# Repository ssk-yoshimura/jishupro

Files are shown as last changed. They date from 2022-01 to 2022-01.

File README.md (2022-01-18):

# 腱之介（けんのすけ）
自主プロ2021のために製作した、ワイヤー駆動ロボット



発表スライド：

https://github.com/ssk-yoshimura/jishupro/blob/master/kennosuke_.pdf

#### アピールポイント

- 6自由度を筋肉10本で動かすロボット（足回り2輪付き）
- 機構を工夫し、安いモータで大きなロボットを動かす（ロボットアーム長0.5m）
- IKを解き、関節角度軌道->ワイヤー長軌道(非線形)を計算して追従&モータの協調動作を実現
- 画像認識も行っている

#### できること
- 歩行（前進、後退、回転）
- 認識（お手）

## メカ構成
基本的に、3Dプリンタとレーザー加工機で製作。骨組み等はホームセンターで入手可能で安価なものを利用。

モータは秋月の連続回転サーボ（エンコーダ付き）FB5311M-360を使用。
- 根本にアクチュエータを集約し、ロボットアームを軽量化
- 肩関節は2自由度3ワイヤー、肘関節は1自由度2ワイヤー
- 両腕と足回り2輪で、合計12個のモータを使用
- モーメントアームを大きくし、減速比を上げてトルクを大きくした。

## 回路構成
- ESP32を使用
- 秋月のI2C接続16チャンネル　サーボ＆ＰＷＭ駆動キットを使用
- 電源は5v4AのACアダプターx2

## ソフトウェア構成
ROSを使用し、IK等にはEusLispを利用した。次のような順番で処理を行っている。

1. (python)Coral TPUからPoseArrayトピックをサブスクライブし、人の姿勢の判別等を行ったり、カメラ画像の色で画像処理を行ったりする。実際はAction Serverとして、呼び出された時のみ処理を行う
3. (euslisp)画像認識の場合はAction Clientとなって利用
4. (euslisp)ロボット手先の軌道を作成
5. (euslisp)手先の軌道をもとにIKを解き、関節角度軌道を作成
6. (euslisp)関節角度軌道から順運動学でワイヤー長軌道を作成(関節角度とワイヤー長は非線形)
7. (euslisp)ワイヤー長軌道と時間、制御パラメータ等をまとめたものを分割し、Float32MultiArrayトピックとしてESP32に送る
8. (ESP32)受信した軌道に欠落がないことを確認し、モータの角度軌道に変換
9. (ESP32)モータの角度軌道をもとに、エンコーダのフィードバックを使って追従制御&協調して動作させる

CAD(SolidWorks)で設計したデータをもとにURDFファイルを作成し、STLを貼り付けた。これを使用して、eusのビューワやRvizでシミュレーションを行った。eusはURDF,yamlから変換してロボットモデルを自動生成した。

#### サーボの初期化
特定の姿勢の状態で、ワイヤーを手動で張り詰めた状態にする。このときのアブソリュートエンコーダの値を読み、サーボ角度とワイヤー長の関係を得る。

使用時は、まずこの初期化のプログラム実行してから、PCとの通信・制御等のプログラムを実行する。

# 発表実演手順
### 準備
```
roscore
```
#### wire_initializeスケッチ
- 電源は外し、init_pinも外して書き込む
- リセットボタンを押す->電源つける->init_pinつける
- シリアルモニタで異常なしを確認、値をコピー
#### wire_pullスケッチ
- コピーした値を貼り付ける
- 電源は外し、init_pinも外して書き込む
- リセットボタンを押す->電源つける->init_pinつける
```
rosrun rosserial_python serial_node.py
```
#### euslisp
jishupro/euslispに入る
```
emacs demo.l
```
シェルを開いて
```
roseus "demo.l
```
```
walk-prepare
```
#### USBカメラ 
ここで初めて、カメラとCoralを付ける。
- フリーズした場合、カメラを挿し直すと改善することがある。

```ls /dev/video```でvideo1があることを確認する。

```
rosrun uvc_camera uvc_camera_node _device:=/dev/video1
```

- PCのカメラの場合```rosrun usb_cam usb_cam_node```

#### Edge TPU 
```
source /opt/ros/melodic/setup.bash
```
```
source ~/coral_ws/devel/setup.bash
```
```
roslaunch coral_usb edgetpu_human_pose_estimator.launch INPUT_IMAGE:=/image_raw
```
#### Action Server
```
python cv_pose_action.py
```
### 発表
#### eusプログラム
- walk-prepare
- walk-both
- walk-back
- rotate
- yc

# リンク集
#### eusモデル、関数など
https://github.com/ssk-yoshimura/jishupro/tree/master/jishupro#readme
#### 諸注意など
https://github.com/ssk-yoshimura/jishupro/tree/master/jishupro/euslisp#readme
#### エンコーダ付き連続回転サーボの処理
https://github.com/ssk-yoshimura/jishupro/tree/master/jishupro/sketch/PCA9685_Sample5#readme

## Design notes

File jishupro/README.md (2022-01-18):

# 腱之介のeusモデル

eusでは```*mbot*```という名前

## 関節
本体側から順
- ```:rarm-shoulder-y```
- ```:rarm-shoulder-p```
- ```:rarm-elbow-p```
- ```:larm-shoulder-y```
- ```:larm-shoulder-p```
- ```:larm-elbow-p```

使用例

```
(send *mbot* :rarm-shoulder-y :joint-angle -30)
```

## 末端
- ```:rarm-end-coords```
- ```:larm-end-coords```

使用例

```
(send *mbot* :rarm-end-coords)
```
または
```
(send *mbot* :rarm :end-coords)
```

## ポーズ
- ```:zero-pose```
- ```:open-pose```
- ```:init-pose``` (サーボ・ワイヤーの初期化用）

使用例

```
(send *mbot* :init-pose)
```
## 関数
重要なもののみ

### ワイヤー関数
```
(load "mbot-utils.l")
(send *mbot* :wire-init) ;; 初期化時に必ず呼ぶ
(send *mbot* :wire-calc) ;; ワイヤー長計算時に必ず呼ぶ
(draw-wire-end) ;; ワイヤー中継地点、関節などを描画
```
### 軌道生成関数
```mbot-ri.l```の関数
```
mbot2ri-avs (avs wheels time_all sequence_mode &key thre_dist goal_offset)
```
引数：関節角度軌道、ホイールの角度軌道、時間、軌道追従の方式、収束判定の閾値、軌道追従のパラメータ

機能：関節角度軌道をワイヤー長軌道に変換し、ESP32に送る

```traj.l```の関数
```
mbot2ri-avs-ik (rtarget ltarget wrtarget wltarget time_all sequence_mode &key thre_dist goal_offset)
```
引数：手のik目標、ホイールの目標、時間、軌道追従の方式、収束判定の閾値、軌道追従のパラメータ

機能：目標をもとにikを解いて軌道を生成し、ESP32に送る

### デモ用の関数
```load "demo.l```でデモに必要な全てのeusプログラムがロードされる
- ```walk-prepare``` 歩行用の姿勢にする
- ```walk-prepare 1```歩行用の姿勢から初期状態へ戻す
- ```walk-both```歩行
- ```walk-back```後ろ向きに歩行
- ```rotate```回転
- ```yc```認識のAction Client（二回行う）

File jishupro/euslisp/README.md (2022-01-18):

## ESP32のプログラム起動の諸注意
- モータの電源を抜き、init_pinを繋げない状態で書き込む。
- リセットボタンを押してから、モータの電源を入れて、その後init_pinを繋げる。
- rosrun rosserial_...する。だめそうだったらリセットボタンからやり直す。
- モータが異常回転している場合、エンコーダの線が抜けている（initialize時にエンコーダの値をよく見て、異常がないことを確認すること）
- 最悪、動画を見せる。

## Coral TPUの諸注意
- カメラ・coralを挿さずにまずesp32のセットアップをする。
- coralはPC（右側）に直接挿す。
- usbカメラはハブのPC側、esp32はハブの先側（横）に挿す。
- 背筋をまっすぐ、少し前屈み。

## 発表
休憩時間に必ずテストランすること。
- 本質にしか触れない
- 2枚目：ワイヤーの話のみ
- 3枚目：おおざっぱに
- 4枚目：位置制御（速度指定サーボ、エンコーダにも軽く触れる）、姿勢推定

## ESP32のプログラム起動がうまくいかないとき
- モータの電源を抜いて試す
- i2cの線を抜く
- リセットボタンを押す
- 替えのESP32を買ってくる
- モータの電源なしでプログラム起動->電源入れる->init_pin入れる
- i2cの線を抜いた状態で書き込み直す
- i2cの5v, GNDを抜いた状態で書き込み直す

- i2cの5v, GNDを抜いた状態で書き込み、これらを挿し戻した後、モータの電源を抜いてリセットボタンを押してから、init_pin, モータ電源の順
- i2cのピンさえ抜いていれば電源はつけたままでよい？

- まともに動かなくなった。
- 買い換える

## esp32でrosを使う手順
### 無線

https://github.com/ssk-yoshimura/jishupro/blob/master/jishupro/sketch/esp_ros_wifi_sample/esp_ros_wifi_sample.ino

スケッチは```Serial.begin(57600)```としておくとラク

PC

```bash
roscore
rosrun rosserial_python serial_node.py tcp
```

次のように表示される
```
[INFO] [1640525677.837441]: ROS Serial Python Node
Fork_server is:  False
[INFO] [1640525677.857589]: Waiting for socket connections on port 11411
waiting for socket connection
```

ここでESP32のENボタンを押すなどして、電源を入れ直す（重要）

少し待つと繋がる
```
[INFO] [1640525688.632853]: Established a socket connection from 192.168.1.17 on port 64560
[INFO] [1640525688.638527]: calling startSerialClient
...
```

### 有線

https://github.com/ssk-yoshimura/jishupro/blob/master/jishupro/sketch/esp32_array_test/esp32_array_test.ino

スケッチで
```c
#undef ESP32
#include <ros.h>
#define ESP32
```
としておくと、```rosrun rosserial_python serial_node.py```で繋がる

```Serial.begin```は書かない（重要）

# jishupro

## eusモデルの作り方
SolidWorksからstlを出力するときは、解像度を下げて、単位をmにする

https://github.com/jsk-ros-pkg/jsk_model_tools

例
```bash
roscd jishupro/models
rosrun collada_urdf_jsk_patch urdf_to_collada sample_model.urdf sample_model.dae
rosrun euscollada collada2eus sample_model.dae sample_model.l
```
https://github.com/ssk-yoshimura/jishupro/tree/master/jishupro/models にMakefileを書いたのでmakeすればできる

## サーボとワイヤーの初期化手順
### 初期設定（一度だけ）
```:init-pose```のときのワイヤー長とサーボ角度を調べて記録する。
#### eusの設定(eusモデル、初期ポーズ変更時以外はやらなくてよい)
```
roseus
(load "mbot-utils.l)
(load "mbot-ri.l")
(send *mbot* :wire-init)
(send *mbot* :init-pose)
(send *mbot* :wire-calc)
(wire-list-to-arduino)
wire-list-arduino
```
これでワイヤー初期長さが表示されるので、wire_pullスケッチのwire_init_pose[]にその値を代入する
#### esp32の設定
- 手動で```:init-pose```の状態にする
  - ここでワイヤーをしっかり張ることが超重要
- wire_initializeスケッチを実行し、シリアルモニタを見る
- エンコーダの値が表示されるので、異常がないことを確認する
- 設定したいサーボの角度を記録する
- wire_pullスケッチのangle_init_pose[]にその値を代入する
### 通常時の設定
- wire_initializeスケッチで、サーボの角度がangle_init_pose +- 50degの範囲にあることを確認する
- 範囲外なら調整して範囲内にし、リセットボタンを押してやり直す
- 範囲外の場合、wire_pullスケッチはwire_init_checkがfalseのままなので動かない。
- (TODO) 範囲外の場合、調整用の角度情報をパブリッシュするようにする

## スケッチ実行時の手順
モータの電源が入っていることを確かめるためにやること
 - wire_initializeやwire_pullスケッチを実行する
 - モータの電源が入っていることを確認する（青いLEDが光る）
 - GPIO2をGNDにつなげる

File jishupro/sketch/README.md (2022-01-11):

1/9夜

1/11試験後にやること

~~スケッチmotor_adjustでrotate_angleとvel2pulseを改良したのでwire_pullに移して試す~~ 1/10やった

~~set_angleは目標変更時にしか呼ばないことを確認する~~ 1/10 OK
- 実際は最初何度も呼んでいるがOK

~~常に位置制御をかけている状態になるのでRdata[i].thetaを初期値とかinit-poseの角度とかで初期化すること~~ 1/10 OK

~~delayを30にする~~ 1/10 OK
- pwmの周波数を上げてもいいかもしれない

サーボ0が動かないバグは直ったので軌道追従がましになってるはず

- プーリーなしの状態で試したら正常に軌道追従するようになった。スピードを下げるタイミングが早くなったので細かい軌道追従だとゆっくりになるかもしれない
- 速さのminの関数の傾きを大きくしてもいいかもしれないが一応これでも動く

motor_adjustでモーターの初期値を調整できるけどあんまり意味がないかも

軌道追従時の次の目標までの距離の閾値(is_near_enoughの不等号の値)をもっと大きくしてもいいかも
- 実際はis_nearestのほうで更新されてそう

↑この値をeusから送るようにして、閾値を変えて色々試す?
- 意味ないかも。やるならis_nearest

目標：1/11で軌道追従をそこそこちゃんとできるようにする！ →プーリーをつけて試す！

## wheel追加 1/11 ##
wheelを追加するにあたってwire_pullを変更した

wheel_motor_numを決める必要がある。

eusでワイヤー長の次にホイール角度[deg]を送るようにする必要がある。

- サーボ関連の定数の一部をサイズ10から12にした
- CB関数で、ワイヤー長の次にホイール角度を受け取るようにした
- wirelenの長さを12にした
- loopの軌道追従にwheel用の処理を追加
- rotate_angleをサーボ12個分処理するようにした
- servo_writeでch=10,11のときwheelを回すようにした
- init_enc_allrange, read_encでwheelのencを読むようにした

## 予定 ##

1/11(火) 軌道追従完成&wheel設計、加工
- 軌道追従完成、wheel設計完成
- esp32側のwheel用プログラムを作成

1/12(水) wheel加工、組立、wheel用のプログラム作成

1/13(木) 前進完成

1/14(金) 動きの追加、認識など

1/15,16 予備

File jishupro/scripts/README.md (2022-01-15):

### 認識 ###

#### USBカメラ ####
```ls /dev/video```でvideo1があることを確認する。

```
rosrun uvc_camera uvc_camera_node _device:=/dev/video1
```

- PCのカメラの場合```rosrun usb_cam usb_cam_node```

#### Edge TPU ####
```
source /opt/ros/melodic/setup.bash
```
```
source ~/coral_ws/devel/setup.bash
```
```
roslaunch coral_usb edgetpu_human_pose_estimator.launch INPUT_IMAGE:=/image_raw
```

#### Human Pose Estimator確認 ####
```
rosrun image_view image_view image:=/edgetpu_human_pose_estimator/output/image
```

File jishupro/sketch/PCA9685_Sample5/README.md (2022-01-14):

## エンコーダ付き連続回転サーボを使う ##

注意：ここで出てくる変数名はプログラムとは一致しません

アブソリュートエンコーダから、モータ角度の情報が、0から360度に対して0〜Lの範囲の整数lで与えられる

モータの角度をx[deg] (0から360度の範囲), xを多回転に拡張したものをtheta[deg]とすると、次の式が成り立つ
```
(1) x = l * 360 / L

(2) theta = x + 360 * n
```

ここで、nはモータの回転が何周目かを表す整数である

### 初期化 ###

setup()でエンコーダを一度読み、その角度をx_0[deg]として保存しておく

n=0としておく

### thetaの更新 ###

エンコーダによって式(1)で求めた角度をxとする。

このとき、thetaおよびnは次のようにして更新できる

```
n_next = argmin_n(|x+360*(n-1)-theta|, |x+360*n-theta|, |x+360*(n+1)-theta|)

theta_next = x + 360 * n_next
```

### 速度の指定 ###

速度wから、[-100, 100]の範囲の値pを計算する（p=-100はpwmのパルス幅1000、p=100がpwmのパルス幅2000に相当し、p=0はpwmのパルス幅1500）

秋月のPCA9685ライブラリで、pを使ってi2cの指令を送る

### 位置制御(簡単ver) ###

目標角度goal[deg]に向かって、角速度wで回転したい

- abs(goal-theta)がある閾値A未満になったら、角速度を0にする。

- abs(goal-theta)がある閾値B(>A)より大きい場合は、角速度wで回す。

- abs(goal-theta)がAからBの範囲にあるときは、制御を行う。
例えば、角速度=k*(theta-goal)とか（P制御）

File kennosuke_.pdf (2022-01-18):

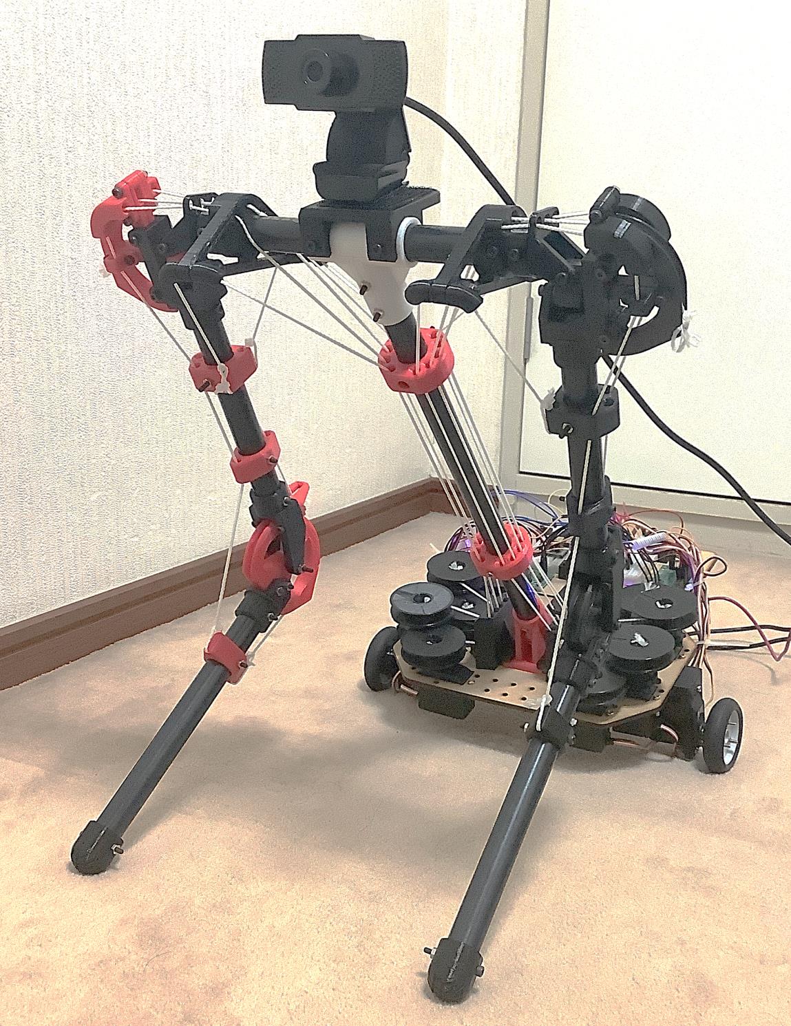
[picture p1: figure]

## ワイヤー駆動ロボット

吉村駿之介

けんのすけ

# 腱之介

スライド1分、実演2分

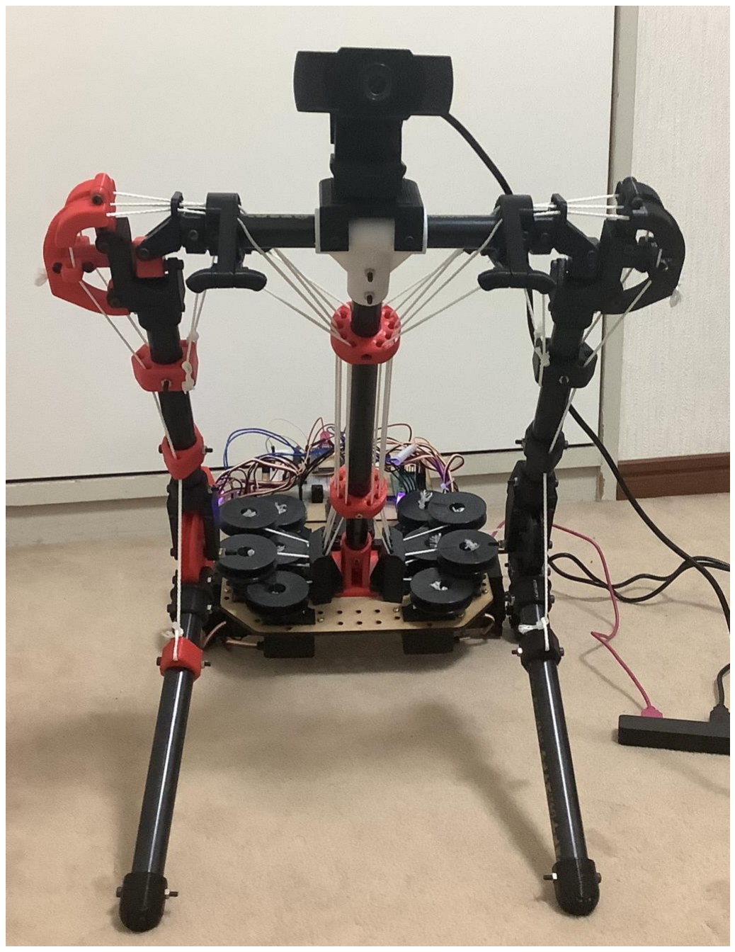
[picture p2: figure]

## 腱之介を一言で表すと…

### •ワイヤー拮抗駆動ロボット犬

- 6自由度を筋肉10本で動かす
- 後ろ足は2輪
- ESP32 + ROS、画像認識(CNNも)

けんのすけ

### 筋肉で動くロボット犬 みたいなものを 作りたい！

## メカ構成

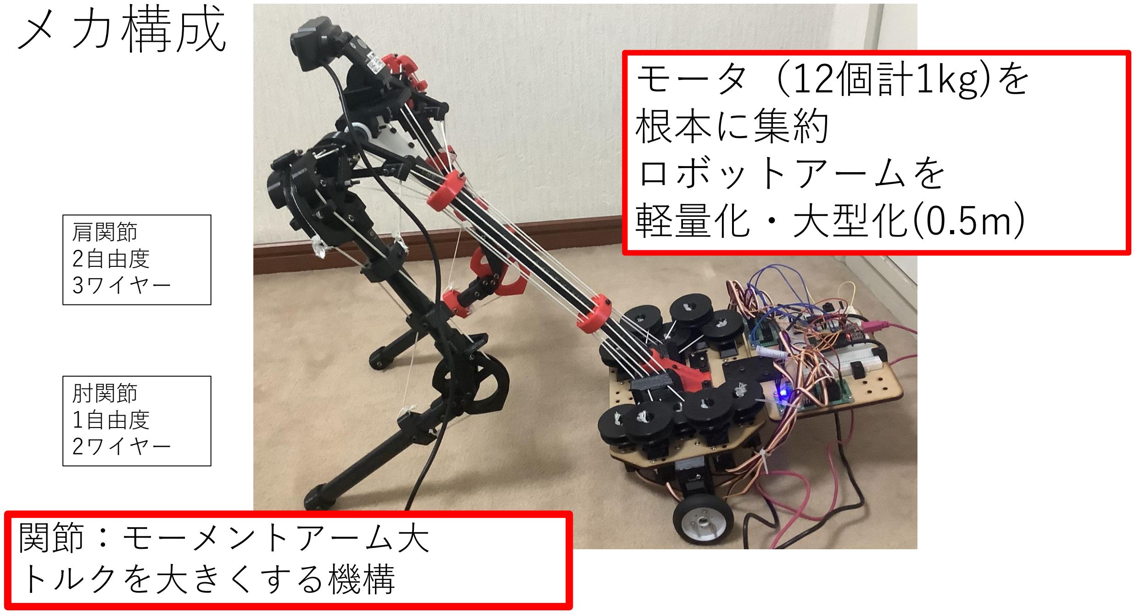
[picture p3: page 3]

肩関節
2自由度
3ワイヤー

モータ（12個計1kg)を
根本に集約
ロボットアームを
軽量化・大型化(0.5m)

肘関節
1自由度
2ワイヤー

関節：モーメントアーム大
トルクを大きくする機構

## ソフトウェア

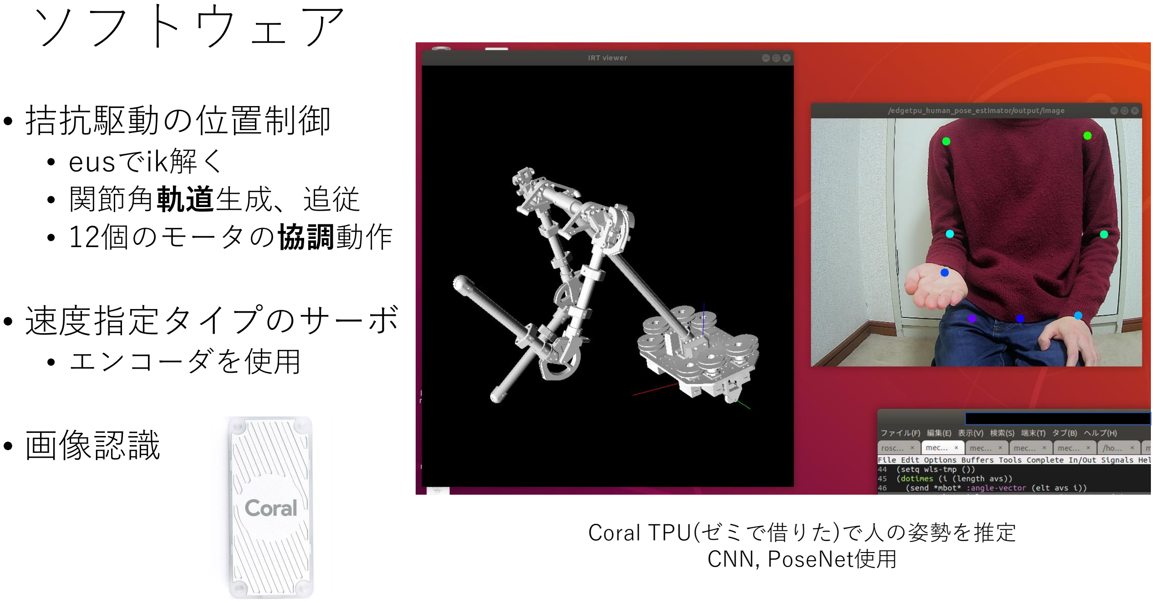
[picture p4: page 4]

- 拮抗駆動の位置制御
- eusでik解く
- 関節角軌道生成、追従
- 12個のモータの協調動作
- 速度指定タイプのサーボ
- エンコーダを使用
- 画像認識

Coral TPU(ゼミで借りた)で人の姿勢を推定
CNN, PoseNet使用

実演

# ① 走行

# 前進、後退、回転

# ② 認識

お手

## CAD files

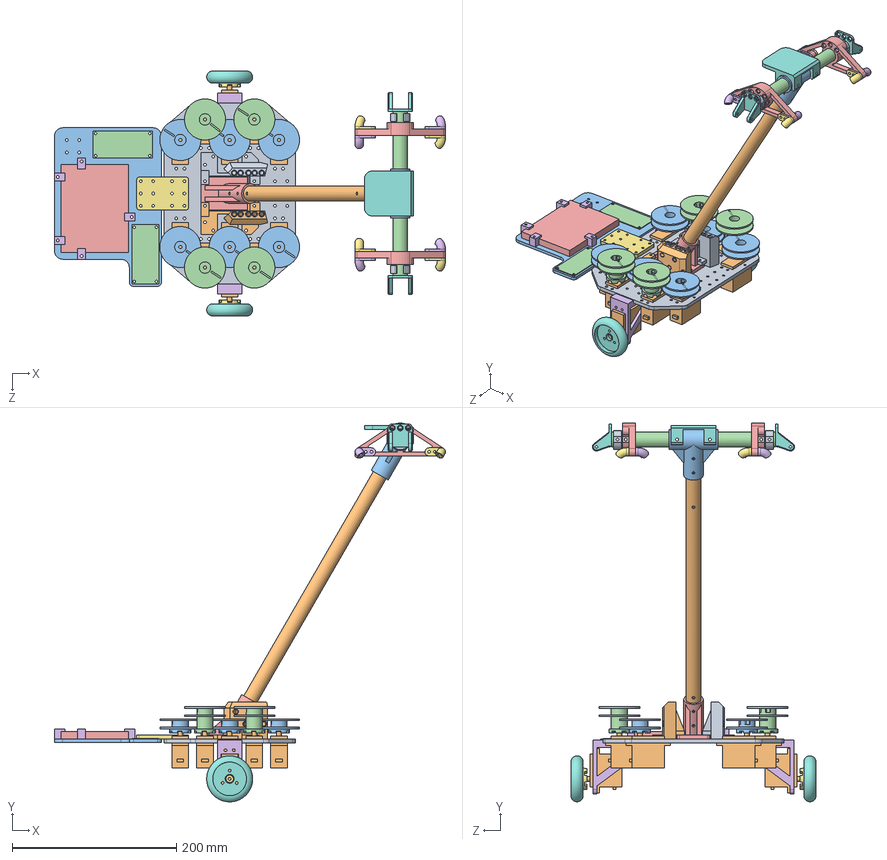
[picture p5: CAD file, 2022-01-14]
CAD/link_root.SLDASM
475.5 x 460.6 x 298.2 mm
base
FB5311M x 12
servo_horn_short x 6
servo_horn_long x 4
connector_45
wheel_motor_mount x 2
wheel_horn x 2
tire x 2
root_connector_loft
pipe_body
connector_T
pipe_shoulder
wire_root_curve x 2
wire_root_curve_support x 4
wire_root_curve_support_mirror x 4
shoulder3 x 2
shoulder_patch x 2
root_connector_loft_mirror
circuit_board
PCA9685 x 2
breadboard
breadboard_support x 5
board_connect
camera_mount

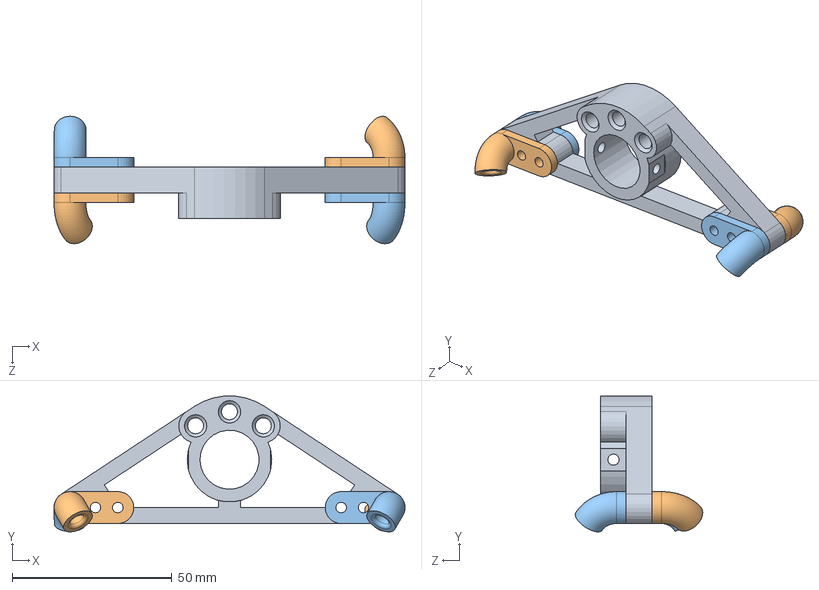
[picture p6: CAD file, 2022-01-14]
CAD/assem_shoulder.SLDASM
110.0 x 42.6 x 40.0 mm
wire_root_curve
wire_root_curve_support x 2
wire_root_curve_support_mirror x 2

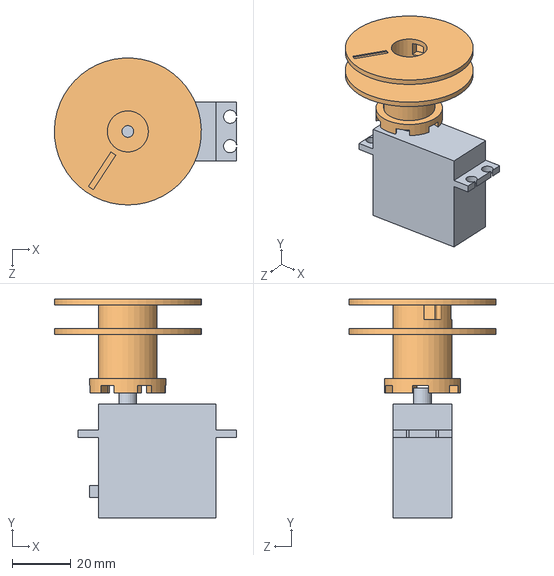
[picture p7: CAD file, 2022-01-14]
CAD/motor_long.SLDASM
62.0 x 74.5 x 50.0 mm
FB5311M
servo_horn_long

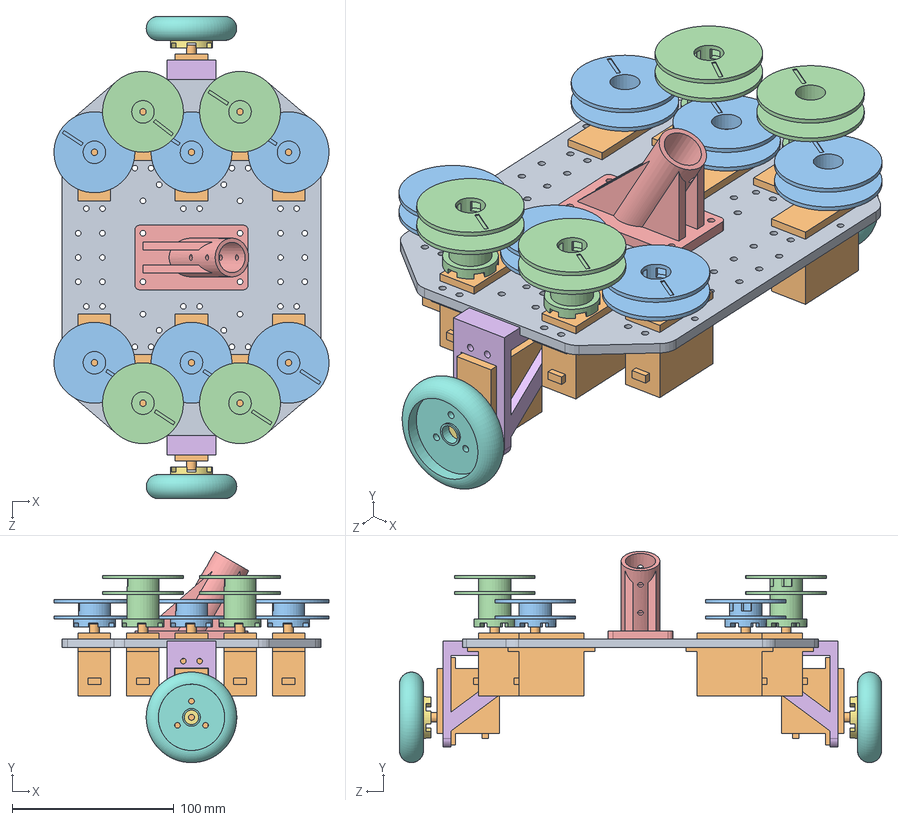
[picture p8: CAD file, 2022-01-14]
CAD/base_motor.SLDASM
170.0 x 130.6 x 298.2 mm
base
FB5311M x 12
servo_horn_short x 6
servo_horn_long x 4
connector_45
wheel_motor_mount x 2
wheel_horn x 2
tire x 2

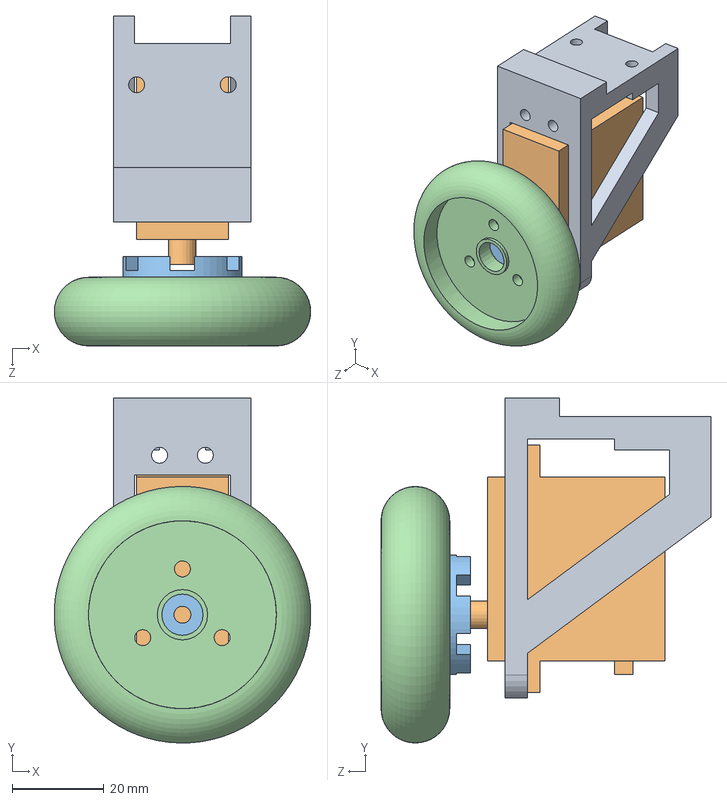
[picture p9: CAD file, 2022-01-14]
CAD/wheel_motor.SLDASM
56.0 x 75.3 x 72.0 mm
wheel_motor_mount
FB5311M
wheel_horn
tire

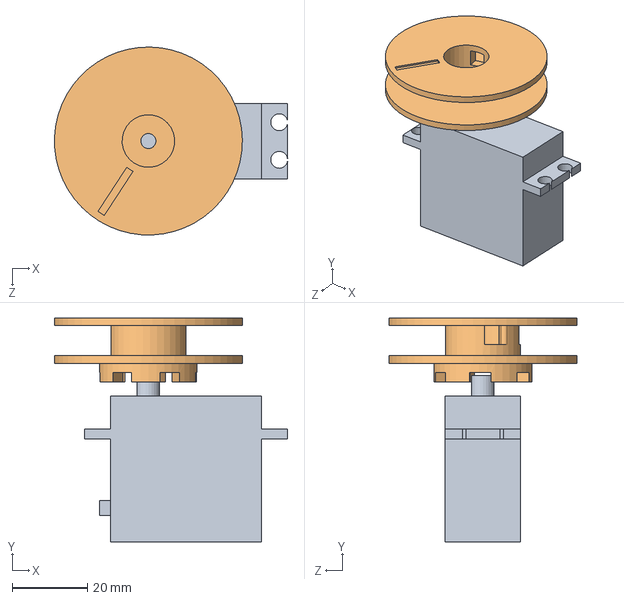
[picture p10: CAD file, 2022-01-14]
CAD/motor.SLDASM
62.0 x 59.5 x 50.0 mm
FB5311M
servo_horn_short

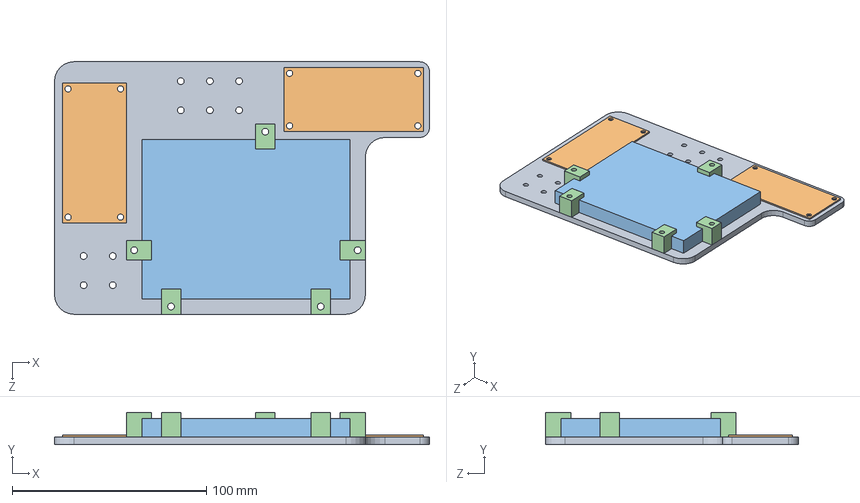
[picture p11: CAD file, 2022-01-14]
CAD/circuit.SLDASM
193.0 x 16.5 x 130.0 mm
circuit_board
PCA9685 x 2
breadboard
breadboard_support x 5

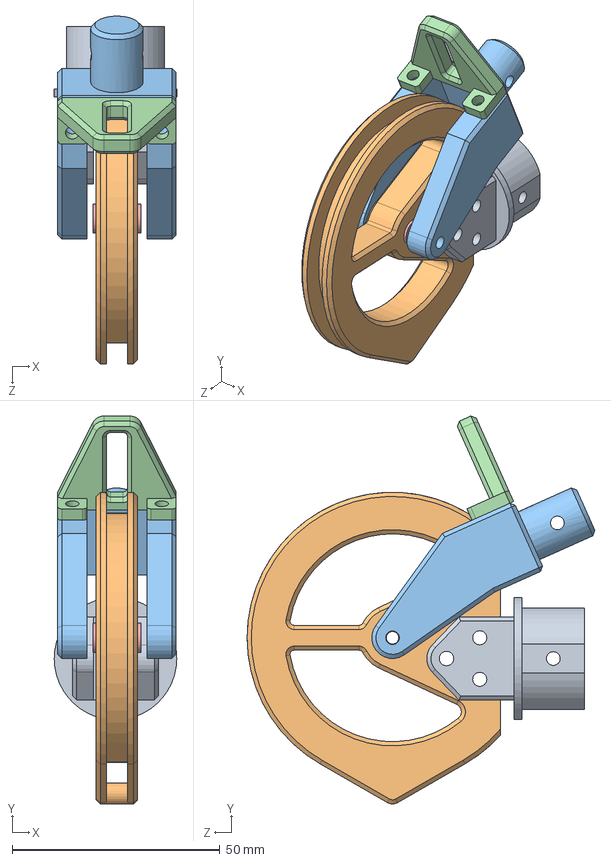
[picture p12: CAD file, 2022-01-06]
CAD/knee.SLDASM
29.5 x 93.4 x 83.7 mm
knee_joint_connector
knee_joint_circle
knee2
knee_support
bearing x 2

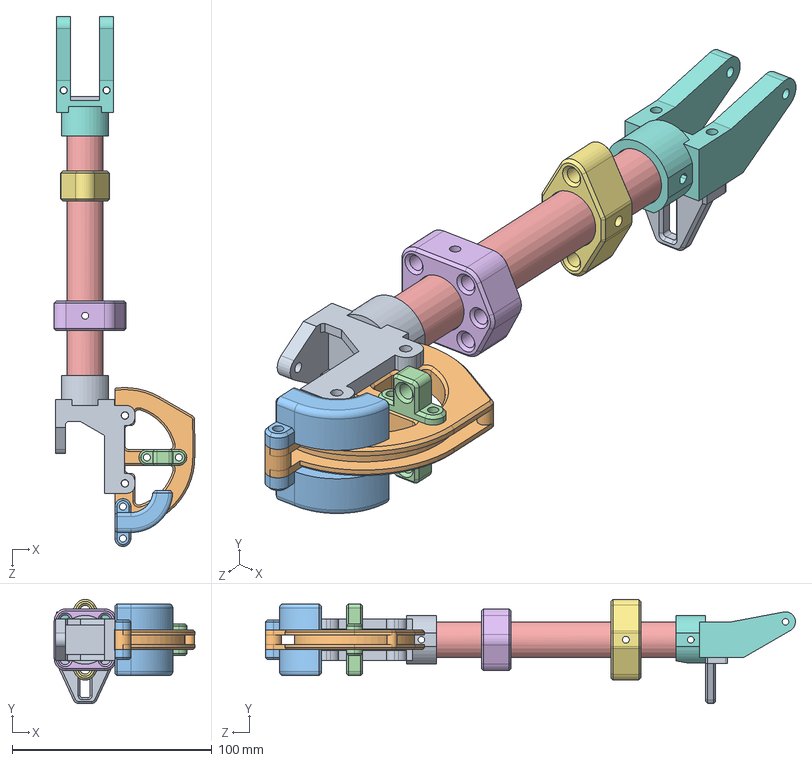
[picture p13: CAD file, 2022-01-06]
CAD/link_leg.SLDASM
70.4 x 52.2 x 265.6 mm
shoulder_joint_connector
shoulder_joint_circle
shoulder_fromknee_middle_curve x 2
shoulder_fromknee_middle x 2
pipe_leg
wire_end_5_small
wire_end_small
knee2
knee_support

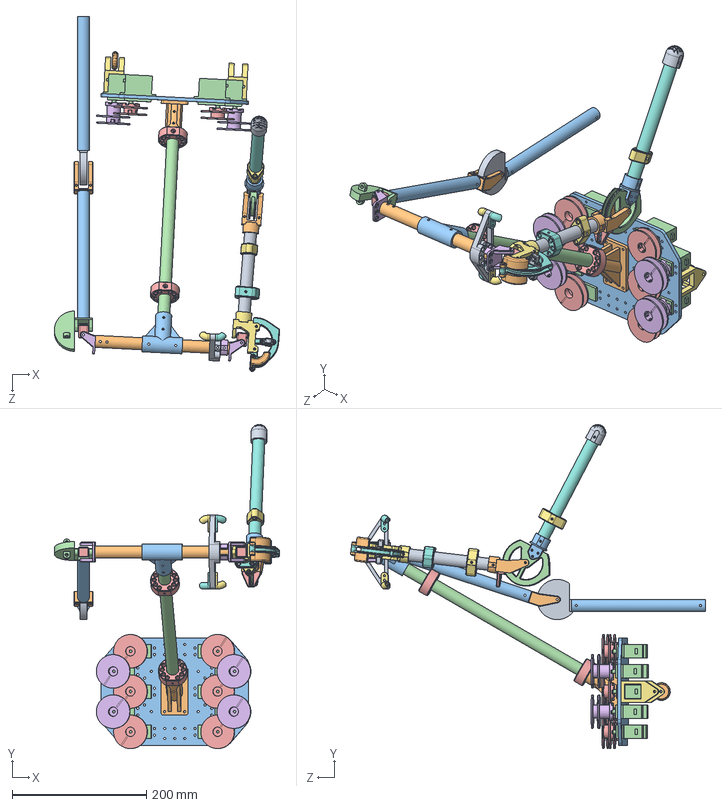
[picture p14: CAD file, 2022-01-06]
CAD/leg.SLDASM
335.8 x 483.0 x 528.9 mm
knee1
knee2 x 2
pipe x 2
shoulder1
shoulder2 x 2
shoulder3 x 2
wire_end_small x 2
wire_end_5_small
wire_root_curve
connector_45 x 2
knee_joint_connector
knee_joint_circle
knee_support
bearing x 6
shoulder_joint_connector
shoulder_joint_circle
shoulder_fromknee_middle x 2
shoulder_fromknee_middle_curve x 2
base
FB5311M x 10
servo_horn_short x 6
servo_horn_long x 4
wheel_support x 2
pipe_foot
pipe_leg
pipe_shoulder
connector_T
pipe_body
wire_from_base_mini x 2
shoulder_patch
wire_root_curve_support x 2
wire_root_curve_support_mirror x 2
foot_simple
wheel

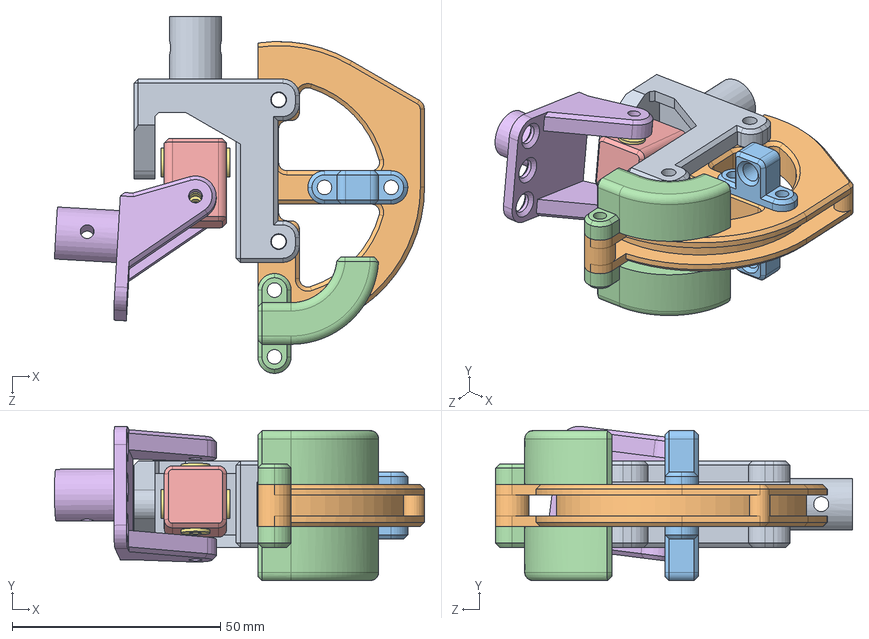
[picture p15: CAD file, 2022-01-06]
CAD/shoulder.SLDASM
88.8 x 37.0 x 85.6 mm
shoulder_joint_connector
shoulder_joint_circle
shoulder_fromknee_middle x 2
shoulder_fromknee_middle_curve x 2
shoulder2
shoulder3
bearing x 4

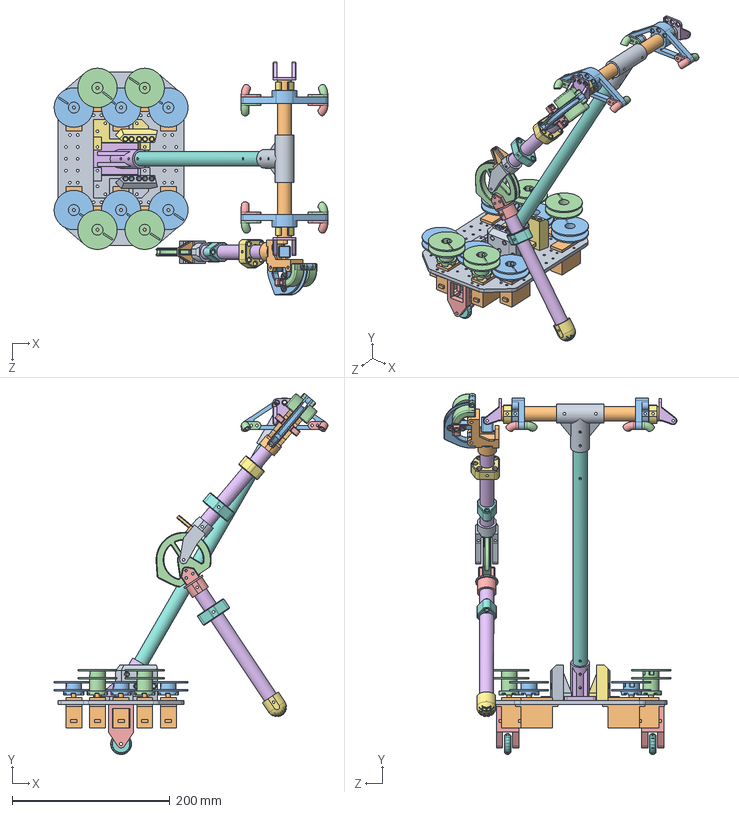
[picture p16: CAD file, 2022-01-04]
CAD/limk_all.SLDASM
347.5 x 458.4 x 296.0 mm
base
FB5311M x 10
servo_horn_short x 6
servo_horn_long x 4
wheel_support x 2
connector_45
root_connector_loft
pipe_body
connector_T
pipe_shoulder
wire_root_curve x 2
wire_root_curve_support x 4
wire_root_curve_support_mirror x 4
shoulder3 x 2
shoulder_patch x 2
wheel x 2
root_connector_loft_mirror
shoulder_joint_connector
shoulder_joint_circle
shoulder_fromknee_middle_curve x 2
shoulder_fromknee_middle x 2
pipe_leg
wire_end_5_small
wire_end_small x 2
knee2
knee_support
shoulder2
knee_joint_circle
knee_joint_connector
pipe_foot
foot_simple

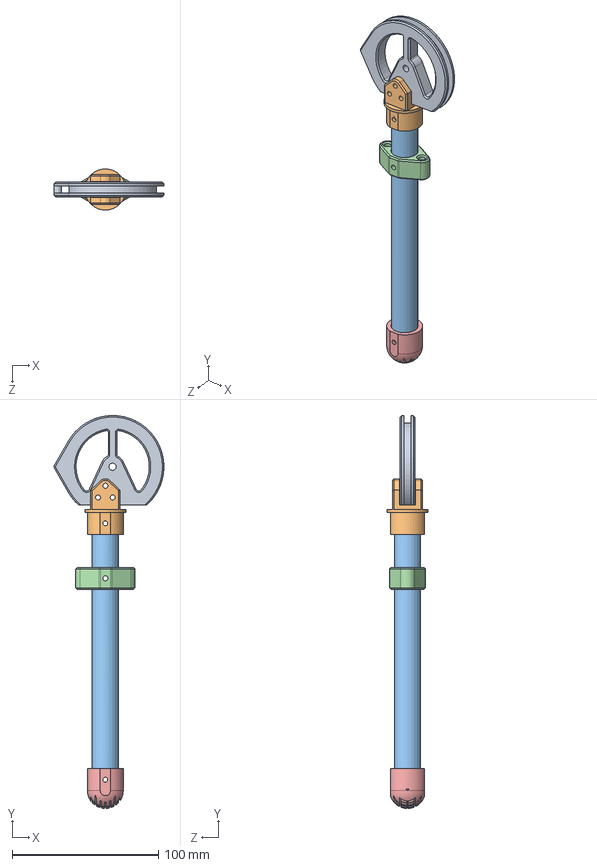
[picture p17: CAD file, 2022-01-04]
CAD/link_foot.SLDASM
75.0 x 268.4 x 28.1 mm
knee_joint_circle
knee_joint_connector
pipe_foot
wire_end_small
foot_simple

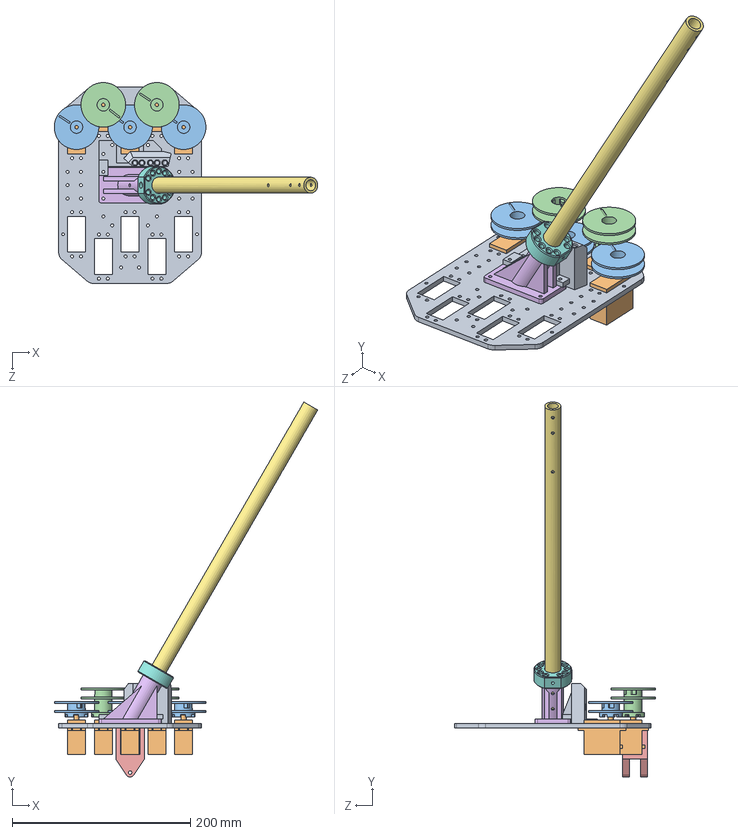
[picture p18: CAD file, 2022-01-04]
CAD/assem_set_motor.SLDASM
295.3 x 420.2 x 225.1 mm
base
FB5311M x 5
servo_horn_short x 3
servo_horn_long x 2
wheel_support
connector_45
pipe_body
wire_from_base_mini
root_connector_loft

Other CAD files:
CAD/link_leg_l.SLDASM
CAD/knees.SLDASM
CAD/model/link_leg_m.STL
CAD/stl/circuit_spacer3.STL
CAD/FB5311M.SLDPRT
CAD/PCA9685.SLDPRT
CAD/base.SLDPRT
CAD/base_wire_connector.SLDPRT
CAD/bearing.SLDPRT
CAD/bearing_try.SLDPRT
CAD/board_connect.SLDPRT
CAD/breadboard.SLDPRT
CAD/breadboard_support.SLDPRT
CAD/camera_mount.SLDPRT
CAD/circuit_board.SLDPRT
CAD/circuit_spacer.SLDPRT
CAD/connector_45.SLDPRT
CAD/connector_T.SLDPRT
CAD/dxf/base.DXF
CAD/dxf/circuit_board.DXF
CAD/foot_simple.SLDPRT
CAD/knee1.SLDPRT
CAD/knee2.SLDPRT
CAD/knee2_trial.SLDPRT
CAD/knee_joint_circle.SLDPRT
CAD/knee_joint_connector.SLDPRT
CAD/knee_support.SLDPRT
CAD/model/link_foot.STL
CAD/model/link_foot_m.STL
CAD/model/link_foot_small.STL
CAD/model/link_leg.STL
CAD/model/link_leg_l.STL
CAD/model/link_leg_small.STL
CAD/model/link_root.STL
CAD/model/shoulder2.STL
CAD/pipe.SLDPRT
CAD/pipe_body.SLDPRT
CAD/pipe_cut.SLDPRT
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

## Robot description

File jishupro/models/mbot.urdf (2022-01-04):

<robot name="mbot">

  <link name="root">
    <inertial>
      <origin xyz="0 0 0" rpy="0 0 0"/>
      <mass value="1"/>
      <inertia ixx="100" ixy="0" ixz="0" iyy="100" iyz="0" izz="100" />
    </inertial>
    <visual>
      <origin xyz="0 0 0" rpy="0 0 0"/>
      <geometry>
	<mesh filename="file:///home/mech-user/jishupro_ws/src/CAD/model/link_root.STL"/>
      </geometry>
    </visual>
  </link>

  <link name="rublock">
    <inertial>
      <origin xyz="0 0 0" rpy="0 0 0"/>
      <mass value="1"/>
      <inertia ixx="100" ixy="0" ixz="0" iyy="100" iyz="0" izz="100" />
    </inertial>
    <visual>
      <origin xyz="0 0 0" rpy="0 0 0"/>
      <geometry>
	<mesh filename="file:///home/mech-user/jishupro_ws/src/CAD/model/shoulder2.STL"/>
      </geometry>
    </visual>
  </link>
  
  <link name="rleg">
    <inertial>
      <origin xyz="0 0 0" rpy="0 0 0"/>
      <mass value="1"/>
      <inertia ixx="100" ixy="0" ixz="0" iyy="100" iyz="0" izz="100" />
    </inertial>
    <visual>
      <origin xyz="0 0 0" rpy="0 0 0"/>
      <geometry>
	<mesh filename="file:///home/mech-user/jishupro_ws/src/CAD/model/link_leg.STL"/>
      </geometry>
    </visual>
  </link>

  <link name="rfoot">
    <inertial>
      <origin xyz="0 0 0" rpy="0 0 0"/>
      <mass value="1"/>
      <inertia ixx="100" ixy="0" ixz="0" iyy="100" iyz="0" izz="100" />
    </inertial>
    <visual>
      <origin xyz="0 0 0" rpy="0 0 0"/>
      <geometry>
	<mesh filename="file:///home/mech-user/jishupro_ws/src/CAD/model/link_foot.STL"/>
      </geometry>
    </visual>
  </link>

  <link name="lublock">
    <inertial>
      <origin xyz="0 0 0" rpy="0 0 0"/>
      <mass value="1"/>
      <inertia ixx="100" ixy="0" ixz="0" iyy="100" iyz="0" izz="100" />
    </inertial>
    <visual>
      <origin xyz="0 0 0" rpy="0 0 0"/>
      <geometry>
	<mesh filename="file:///home/mech-user/jishupro_ws/src/CAD/model/shoulder2.STL"/>
      </geometry>
    </visual>
  </link>
  
  <link name="lleg">
    <inertial>
      <origin xyz="0 0 0" rpy="0 0 0"/>
      <mass value="1"/>
      <inertia ixx="100" ixy="0" ixz="0" iyy="100" iyz="0" izz="100" />
    </inertial>
    <visual>
      <origin xyz="0 0 0" rpy="0 0 0"/>
      <geometry>
	<mesh filename="file:///home/mech-user/jishupro_ws/src/CAD/model/link_leg_l.STL"/>
      </geometry>
    </visual>
  </link>

  <link name="lfoot">
    <inertial>
      <origin xyz="0 0 0" rpy="0 0 0"/>
      <mass value="1"/>
      <inertia ixx="100" ixy="0" ixz="0" iyy="100" iyz="0" izz="100" />
    </inertial>
    <visual>
      <origin xyz="0 0 0" rpy="0 0 0"/>
      <geometry>
	<mesh filename="file:///home/mech-user/jishupro_ws/src/CAD/model/link_foot.STL"/>
      </geometry>
    </visual>
  </link>

  <joint name="root2rublock" type="revolute">
    <parent link="root"/>
    <child link="rublock"/>
    <origin xyz="0.2075 -0.118 0.4104" rpy="0 0 0"/>
    <axis xyz="1 0 0"/>
    <limit effort="1000.0" lower="-1.5" upper="1.5" velocity="0.5"/>
  </joint>

  <joint name="rublock2rleg" type="revolute">
    <parent link="rublock"/>
    <child link="rleg"/>
    <origin xyz="0 0 -0.010" rpy="0 0 0"/>
    <axis xyz="0 1 0"/>
    <limit effort="1000.0" lower="-1.5" upper="1.5" velocity="0.5"/>
  </joint>

  <joint name="rleg2rfoot" type="revolute">
    <parent link="rleg"/>
    <child link="rfoot"/>
    <origin xyz="0.009 0 -0.210" rpy="0 0 0"/>
    <axis xyz="0 1 0"/>
    <limit effort="1000.0" lower="-2.72" upper="1.5" velocity="0.5"/>
  </joint>

  <joint name="root2lublock" type="revolute">
    <parent link="root"/>
    <child link="lublock"/>
    <origin xyz="0.2075 0.118 0.4104" rpy="0 0 0"/>
    <axis xyz="1 0 0"/>
    <limit effort="1000.0" lower="-1.5" upper="1.5" velocity="0.5"/>
  </joint>

  <joint name="lublock2lleg" type="revolute">
    <parent link="lublock"/>
    <child link="lleg"/>
    <origin xyz="0 0 -0.010" rpy="0 0 0"/>
    <axis xyz="0 1 0"/>
    <limit effort="1000.0" lower="-1.5" upper="1.5" velocity="0.5"/>
  </joint>

  <joint name="lleg2lfoot" type="revolute">
    <parent link="lleg"/>
    <child link="lfoot"/>
    <origin xyz="0.009 0 -0.210" rpy="0 0 0"/>
    <axis xyz="0 1 0"/>
    <limit effort="1000.0" lower="-2.72" upper="1.5" velocity="0.5"/>
  </joint>
    
</robot>

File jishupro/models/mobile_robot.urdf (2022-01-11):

<?xml version="1.0" ?>
<robot name="mobilerobot">
  <material name="black">
    <color rgba="0.2 0.2 0.2 1"/>
  </material>
  <material name="grey">
    <color rgba="0.75 0.75 0.75 1"/>
  </material>
  <link name="base_link">
    <visual>
      <geometry>
        <mesh filename="package://mobile_robot_description/meshes/raspi_mouse_body.stl"/>
      </geometry>
      <material name="grey"/>
      <origin xyz="-0.041 -0.05 -0.02575" rpy="0 0 0"/>
    </visual>
    <visual name="regulators">
      <geometry>
        <box size="0.005 0.065 0.02"/>
      </geometry>
      <origin xyz="0.04 0 0.036" rpy="0 0 0"/>
      <material name="black"/>
    </visual>
    <visual name="connector">
      <geometry>
        <box size="0.075 0.016 0.026"/>
      </geometry>
      <origin xyz="0 -0.027 0.039" rpy="0 0 0"/>
      <material name="black"/>
    </visual>
    <collision>
      <geometry>
        <box size="0.13 0.1 0.078"/>
      </geometry>
      <origin xyz="0 0 0.013" rpy="0 0 0"/>
    </collision>
  </link>

  <link name="caster_support">
    <visual>
      <geometry>
        <mesh filename="package://mobile_robot_description/meshes/mobile_robot_caster.stl"/>
      </geometry>
      <origin xyz="0 0 0" rpy="0 0 0"/>
      <material name="grey"/>
    </visual>
    <collision>
      <geometry>
        <box size="0.04 0.009 0.025"/>
      </geometry>
      <origin xyz="-0.015 0 0" rpy="0 0 0"/>
    </collision>
  </link>

  <joint name="caster_support_joint" type="continuous">
    <axis xyz="0 0 1"/>
    <parent link="base_link"/>
    <child link="caster_support"/>
    <origin xyz="-0.065 0 -0.01" rpy="0 0 0"/>
  </joint>

  <link name="caster_wheel">
    <visual>
      <geometry>
        <cylinder length="0.005" radius="0.02"/>
      </geometry>
      <material name="black"/>
    </visual>
    <collision>
      <geometry>
        <cylinder length="0.005" radius="0.02"/>
      </geometry>
    </collision>
  </link>

  <joint name="caster_wheel_joint" type="continuous">
    <axis xyz="0 0 1"/>
    <parent link="caster_support"/>
    <child link="caster_wheel"/>
    <origin xyz="-0.02 0 -0.02" rpy="-1.5708 0 0"/>
  </joint>

  <link name="right_wheel">
    <visual>
      <geometry>
        <cylinder length="0.008" radius="0.024"/>
      </geometry>
      <material name="black"/>
    </visual>
    <collision>
      <geometry>
        <cylinder length="0.008" radius="0.024"/>
      </geometry>
    </collision>
  </link>

  <joint name="right_wheel_joint" type="continuous">
    <axis xyz="0 0 1"/>
    <parent link="base_link"/>
    <child link="right_wheel"/>
    <origin xyz="0 0.054 -0.021" rpy="-1.5708 0 0"/>
  </joint>

  <link name="left_wheel">
    <visual>
      <geometry>
        <cylinder length="0.008" radius="0.024"/>
      </geometry>
      <material name="black"/>
    </visual>
    <collision>
      <geometry>
        <cylinder length="0.008" radius="0.024"/>
      </geometry>
    </collision>
  </link>

  <joint name="left_wheel_joint" type="continuous">
    <axis xyz="0 0 1"/>
    <parent link="base_link"/>
    <child link="left_wheel"/>
    <origin xyz="0 -0.054 -0.021" rpy="-1.5708 0 0"/>
  </joint>

  <link name="laser">
    <visual>
      <geometry>
        <box size="0.05 0.05 0.05"/>
      </geometry>
      <material name="red">
        <color rgba="0.9 0.1 0.1 1"/>
      </material>
    </visual>
    <collision>
      <geometry>
        <box size="0.05 0.05 0.05"/>
      </geometry>
    </collision>
  </link>

  <joint name="laser_joint" type="fixed">
    <parent link="base_link"/>
    <child link="laser"/>
    <origin xyz="0 0 0.051" rpy="0 0 0"/>
  </joint>
</robot>

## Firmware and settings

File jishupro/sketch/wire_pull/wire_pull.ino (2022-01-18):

#include <Wire.h>
#include <PCA9685.h>            //PCA9685用ヘッダーファイル（秋月電子通商作成）
#undef ESP32
#include <ros.h>
#define ESP32
#include <std_msgs/Float32MultiArray.h>
//#include <std_msgs/Int32.h>

PCA9685 pwm = PCA9685(0x40);    //PCA9685のアドレス指定（アドレスジャンパ未接続時）
PCA9685 pwm2 = PCA9685(0x41);


// パルスの割合
// 4096がmax
// パルス幅1000-2000usecが動く範囲
#define SERVOMIN 246            //最小パルス幅 (標準的なサーボパルスに設定)
#define SERVOMAX 492            //最大パルス幅 (標準的なサーボパルスに設定)

const int n=10; // サーボのこすう

const int init_pin = 2; // サーボ初期化スイッチ入力
int servo_zero[12]; // サーボの初期角度
int servo_n[12]; // サーボのかいてんすう、最初0をかていする
int enc[12]; // エンコーダの値
int enc_raw[12]; // エンコーダの生の値
float angle[12]; // 角度 deg
bool init_done = false;
const int maxV = 4096;

// deg/s
float vel_limit_max[12] = {16.0,12.0,17.0,18.0,17.5,16.0,16.0,16.0,16.0,16.0, 16.0, 16.0};
float vel_limit_min[12] = {-20,-20,-16,-15,-20,-20,-20,-20,-20,-20, -20, -20};
// pulse (-100 to 100)
int pulse_limit_max[12] = {17,16,18,16,16,17,17,17,17,17,17,17}; 
int pulse_limit_min[12] = {-7,-6,-8,-8,-7,-8,-8,-8,-8,-8,-8,-8};
// grad : vel / pulse
float k_p[12] = {3.9, 3.7, 3.7, 3.8, 3.9, 3.7, 3.7, 3.7, 3.7, 3.7, 3.7, 3.7};
float k_m[12] = {3.7, 3.9, 3.3, 3.6, 3.7, 3.7, 3.7, 3.7, 3.7, 3.7, 3.7, 3.7};

int set_angle_count[12];
void set_angle(int ch, float vel, float theta, float cthre=10.0, float thre=5.0);
void rotate_angle();
struct rotate_data{
  float vel; //set vel
  float theta;
  float cthre;
  float thre;
  float dangle=0.0; 
  float rvel=0.0; //real vel
};

rotate_data Rdata[12];

float wire2angle(int ch, float w);
float angle2wire(int ch, float agl);

float vels[30]; // 速度測定用

/*
const int s0 = 32;
const int s1 = 25;
const int s2 = 34;
const int s3 = 39;
const int SIG_PIN = 36;
*/

//const int enc_pin[10] = {36, 39, 34, 35, 32, 14, 27, 26, 25, 33};
const int enc_pin[10] = {36, 39, 34, 35, 32, 33, 25, 26, 27, 14};

const int wheel_enc_pin[2] = {4, 0};

const int wheel_motor_num[2] = {7 , 7};


ros::NodeHandle nh;
std_msgs::Float32MultiArray wirelen;
ros::Publisher p("arduino", &wirelen);
float wire_list_goal[10];

// cvg
//std_msgs::Int32 cvg;
//ros::Publisher pc("cvg", &cvg);

//init-poseのときのwire-list-arduino
// eusで計算する(:wire-calc後にwire-list-to-arduinoする)
const float wire_init_pose[10] = {
  82.0293, 49.619, 34.055, 262.47, 61.8248,
  82.0293, 49.619, 34.055, 262.47, 61.8248
};

// init-poseのときのangle
// wire_initializeで求める
const float angle_init_pose[10] = {
  //349.28, 279.32, 24.96, 147.57, 177.28, 289.95, 115.93, 4.13, 359.91, 60.47
  //350.07, 282.66, 19.07, 148.62, 205.22, 291.88, 119.53, 15.91, 359.91, 60.64
  //330.12, 248.73, 26.02, 185.63, 186.24, 242.49, 154.95, 0.00, 313.51, 44.03
  //334.25, 255.41, 18.54, 179.38, 186.24, 240.56, 150.12, 3.25, 313.07, 43.15
  // 359.91, 265.78, 16.87, 163.74, 174.55, 58.71, 140.80, 3.60, 326.25, 65.21  
  //359.91, 268.07, 14.15, 162.86, 174.99, 67.85, 140.54, 2.99, 325.02, 64.69 
  //359.91, 267.98, 15.12, 163.65, 174.29, 256.11, 140.36, 3.69, 326.25, 64.78
  // 359.91, 258.31, 13.18, 154.86, 181.58, 267.36, 151.44, 0.00, 302.78, 77.34 
  337.94, 266.75, 5.45, 166.20, 194.85, 270.44, 164.88, 359.91, 281.34, 83.58 
};

// サーボ回転角の係数
// pull when counterclockwise : 1
// pull when clockwise : -1
const int pull_direction[10] = {
  1,1,-1,-1,-1,
  -1,-1,1,1,1
};

const float forward_direction[2] = {1.0, -1.0};

float wire_list[10];

// servo check
bool wire_init_check = false;

// pulley radius
const float r_pulley = 11.0;

//wheel radius
const float r_wheel = 26.0;

// ここでワイヤー長さを得て、角度を制御する
void messageCb(const std_msgs::Float32MultiArray& msg){
  for(int i=0;i<msg.data_length;i++){
    wire_list_goal[i] = msg.data[i];
    // wirelen.data[i] = wire_list_goal[i];
  }
}

float goal_sequence[30][15]; // (idx, time, wl, wangle)
int goal_sequence_length = 0;
int get_sequence_state = 0; //0:no 1:getting 2:moving
int get_sequence_count = 0;
int seq_test = 0;
int seq_crt_idx = 0;
int goal_offset = 0;
int goal_override = 0; // goal override counter

float sequence_mode = 0.0;
float thre_dist = 5.0; //mm

float wheel_initial_angle[2]; // use when calculate wheel rotation goal

// angle-vector-sequence用
void messageCbsequence(const std_msgs::Float32MultiArray& msg){
  if(msg.data[0] == 0.0){ // 受信開始
    get_sequence_state = 1;
    get_sequence_count = 0;
    goal_sequence_length = 0;
    goal_override = 0;
    //cvg.data = 0;
    for(int i=0;i<30;i++){
      goal_sequence[i][0] = 0.0;
      goal_sequence[i][1] = 0.0;
    }
  }
  if(get_sequence_state == 1){ // 受信
    //seq_test++;
    if(msg.data[1] == -99){ //終了 & move start
      goal_sequence_length = msg.data[0];
      goal_offset = msg.data[2];
      sequence_mode = msg.data[3];
      thre_dist = msg.data[4];
      
      get_sequence_state = 2;
      seq_crt_idx = 0;
    }
    for(int i=0;i<msg.data_length;i++){
      goal_sequence[get_sequence_count][i] = msg.data[i];
      //debug
      if(i >= 2){
        //wirelen.data[i-2] = goal_sequence[get_sequence_count][i];
      }
    }
    if(get_sequence_count != (int)goal_sequence[get_sequence_count][0]){ //値が飛んだとき
      get_sequence_state = 0;
    }
    get_sequence_count++;
  }
}

ros::Subscriber<std_msgs::Float32MultiArray> s("wireus", messageCb);
ros::Subscriber<std_msgs::Float32MultiArray> seq("wire_sequence", messageCbsequence);

void setup() {
 // Serial.begin(57600);
 pwm.begin();                   //初期設定 (アドレス0x40用)
 pwm.setPWMFreq(60);            //PWM周期を60Hzに設定 (アドレス0x40用)
 pwm2.begin();
 pwm2.setPWMFreq(60);
 pinMode(init_pin, INPUT_PULLUP);
 for(int i=0;i<n;i++){
  wire_list_goal[i] = wire_init_pose[i];
  set_angle(i, 50, wire2angle(i, wire_init_pose[i])); // set only, not rotate
  servo_write(i, 0); // stop servo
 }
 for(int i=10;i<12;i++){ // stop wheel
  servo_write(i, 0);
 }
 nh.initNode();
 wirelen.data = (float*)malloc(sizeof(float) * 12);
 wirelen.data_length = 12;
 //cvg.data = 0;
 for(int i=0;i<wirelen.data_length;i++){
  wirelen.data[i] = 123.0;
 }
 nh.advertise(p);
 // nh.subscribe(s);
 nh.subscribe(seq);

 while(!init_done){
    //init_enc();
    init_enc_allrange();
 }
 for(int i=10;i<12;i++){
  set_angle(i, 50, angle[i]);
 }
 wirelen.data[0] = 88.0;
}

// -100から100にできないか -> できた
// 時計回りが正

int a = 0;
int b = 0;

// 
void loop() {
  read_enc();
  if(!wire_init_check){
     for(int i=0;i<wirelen.data_length;i++){
        wirelen.data[i] = -99.0;
     } 
     wirelen.data[0] = (float)goal_sequence_length;
    p.publish(&wirelen);
    nh.spinOnce();
    delay(100);
    return;
  }
  // angle-vector
  // use only wire_list_goal
  /*
  for(int i=0;i<n;i++){ // wire
    float angle_goal = wire2angle(i, wire_list_goal[i]); // wire_list_goalからangleを求める
    set_angle(i, 100.0, angle_goal);
    // wirelen.data[i] = angle2wire(i, angle[i]); // 現在の長さ
    // wirelen.data[i] = wire_list_goal[i]; // 目標の長さ
    wirelen.data[i] = wire_list_goal[i] - angle2wire(i, angle[i]); // 現在と目標の差分
  }
  */
  for(int i=0;i<n;i++){
    //wirelen.data[i] = angle2wire(i, angle[i]); // publish current wire length
  }
  // debug
   //wirelen.data[0] = seq_crt_idx;
   //wirelen.data[1] = (float)goal_sequence_length;
  // angle-vector-sequence
  // use goal_sequence (idx, t, (wl)) and goal_sequence_length
  // start when get_sequence_state == 2
  // current next idx: seq_crt_idx
  if(get_sequence_state == 2){
    if(seq_crt_idx == 0){
      // first : angle vector
      // set pulley to first position
      // wheel: not move and get initial position
      float wl_err_max = 0.0;
      for(int i=0;i<n;i++){ //pulley
        float angle_goal = wire2angle(i, goal_sequence[0][i+2]);
        set_angle(i, 80.0, angle_goal);
        wl_err_max = max(wl_err_max, abs(goal_sequence[0][i+2]-angle2wire(i, angle[i])));
      }
      for(int i=0;i<2;i++){ // wheel
        wheel_initial_angle[i] = angle[i+10]; // set wheel initial angle
        set_angle(i+10, 50.0, angle[i+10]);
      }
      if(wl_err_max < 1.0){
        seq_crt_idx = 1;
        // set first pulley goal
        for(int i=0;i<n;i++){
          float seq_t = goal_sequence[1+goal_offset][1] - goal_sequence[0][1];
          float seq_l = abs(goal_sequence[1+goal_offset][i+2] - angle2wire(i, angle[i]));
          set_angle(i, seq_l / (seq_t * r_pulley) * (180.0 / PI), wire2angle(i, goal_sequence[1+goal_offset][i+2]));
        }
        // set first wheel goal
        for(int i=0;i<2;i++){
          float seq_t = goal_sequence[1+goal_offset][1] - goal_sequence[0][1];
          float seq_theta = abs(goal_sequence[1+goal_offset][i+12]); // deg
          float wheel_goal = forward_direction[i] * goal_sequence[1+goal_offset][i+12] + wheel_initial_angle[i];
          set_angle(i+10, seq_theta / seq_t, wheel_goal);
        }
      }
    }
    if(seq_crt_idx > 0 && seq_crt_idx < goal_sequence_length-1){
      // update goal or not
      bool seq_update = true;
      for(int i=0;i<n;i++){ // pulley convergence check
        float wl_distance_next = abs(goal_sequence[seq_crt_idx][i+2]-angle2wire(i, angle[i]));
        float wl_distance_prev = abs(goal_sequence[seq_crt_idx-1][i+2]-angle2wire(i, angle[i]));
        
        // goal update algorithm
        // sequence_mode 0: use is_near_enough and is_nearest
        // sequence_mode 1: use only is_near_enough, use thre_dist[deg]
        // goal_offset 0 is recommended
        if((int)sequence_mode == 0){
          bool is_near_enough = (wl_distance_next < 1.0);
          bool is_nearest = (wl_distance_next < wl_distance_prev);
          seq_update &= (is_near_enough || is_nearest);
        }else if((int)sequence_mode == 1){
          bool is_near_enough = (wl_distance_next < thre_dist);
          seq_update &= is_near_enough;
        }
      }
      for(int i=0;i<2;i++){ // wheel convergence check, use only is_near_enough algorithm
        float wheel_goal = forward_direction[i] * goal_sequence[seq_crt_idx][i+12] + wheel_initial_angle[i];
        float angle_distance = abs(wheel_goal - angle[10+i]);
        float wheel_thre = thre_dist * 180.0 / (PI * r_pulley);
        seq_update &= (angle_distance < wheel_thre);
      }
      if(seq_update){
        for(int i=0;i<n;i++){ // pulley goal update
          // using current angle
          /*
          int goal_idx_next = min(seq_crt_idx+1+goal_offset, goal_sequence_length-1);
          float seq_t = goal_sequence[goal_idx_next][1] - 
            0.5*(goal_sequence[seq_crt_idx][1]-goal_sequence[seq_crt_idx-1][1]);
          float seq_l = abs(goal_sequence[goal_idx_next][i+2] - angle2wire(i, angle[i]));
          set_angle(i, seq_l / (seq_t * r_pulley) * (180.0 / PI) , wire2angle(i, goal_sequence[seq_crt_idx+1][i+2]));
          */
          // not use current angle when decide vel, use only goal value
          int goal_idx_next = min(seq_crt_idx+1+goal_offset, goal_sequence_length-1);
          float seq_t = goal_sequence[goal_idx_next][1] - goal_sequence[goal_idx_next-1][1];
          float seq_l = abs(goal_sequence[goal_idx_next][i+2] - goal_sequence[goal_idx_next-1][i+2]);
          set_angle(i, seq_l / (seq_t * r_pulley) * (180.0 / PI), wire2angle(i, goal_sequence[goal_idx_next][i+2]));
        }
        for(int i=0;i<2;i++){ //wheel goal update
          ///*
          int goal_idx_next = min(seq_crt_idx+1+goal_offset, goal_sequence_length-1);
          float seq_t = goal_sequence[goal_idx_next][1] - goal_sequence[goal_idx_next-1][1];
          float seq_theta = abs(goal_sequence[goal_idx_next][i+12] - goal_sequence[goal_idx_next-1][i+12]);
          float wheel_goal = forward_direction[i] * goal_sequence[goal_idx_next][i+12] + wheel_initial_angle[i];
          set_angle(i+10, seq_theta / seq_t, wheel_goal);
        }
        seq_crt_idx++;
      }
    }
    if(seq_crt_idx == goal_sequence_length-1){
      get_sequence_state = 0; // 終了
      // seq_crt_idx : last goal idx
      goal_override = 1; // goal_override count start
    }
  }
  rotate_angle(); // call in every loop
  /*
  for(int i=0;i<5;i++){ // debug
    wirelen.data[i] = Rdata[i].rvel;
    wirelen.data[i+5] = Rdata[i].dangle;
  }
  */
  
  wirelen.data[0] = seq_crt_idx;
  wirelen.data[10] = Rdata[10].rvel;
  wirelen.data[11] = Rdata[11].rvel;
  
  p.publish(&wirelen);
  nh.spinOnce();
  delay(30);  
}


// vel[deg/s] to pulse in (-100,100)
int vel2pulse(int ch, float vel){
  int pulse = 0;
  if(vel >= vel_limit_max[ch]){
    pulse = pulse_limit_max[ch];
    pulse += (int)((vel - vel_limit_max[ch]) / k_p[ch]);
  }else if(vel <= vel_limit_min[ch]){
    pulse = pulse_limit_min[ch];
    pulse += (int)((vel - vel_limit_min[ch]) / k_m[ch]);
  }
  return pulse;
}

// set servo to theta, vel > 0
// use in loop
// thre: end threshold
// cthre: control start threshold
void set_angle(int ch, float vel, float theta, float cthre, float thre){
  // default
  // cthre = 10.0;
  // thre = 5.0;
  Rdata[ch].vel = vel;
  Rdata[ch].theta = theta;
  Rdata[ch].cthre = cthre;
  Rdata[ch].thre = thre;
}

void rotate_angle(){
  // goal_override
  if(goal_override > 0){
    bool goal_override_check = true;
    for(int i=0;i<12;i++){
      float dist = Rdata[i].theta - angle[i];
      goal_override_check &= (abs(dist) < 10.0);
    }
    if(goal_override_check){
      goal_override++;
    }
    if(goal_override > 50){ // goal override
      for(int i=0;i<12;i++){
        Rdata[i].theta = angle[i];
      }
      goal_override = 0;
      //cvg.data = 1;
    }
  }

  // rotate angle
  for(int ch=0;ch<12;ch++){

    float vel = Rdata[ch].vel;
    float theta = Rdata[ch].theta;
    float cthre = Rdata[ch].cthre;
    float thre = Rdata[ch].thre;
    
    // 安全
    if(vel < 0)vel *= -1.0;
    if(vel > 200) vel = 200;
    if(vel < 25) vel = 25;

    float dist = theta - angle[ch];

    Rdata[ch].dangle = dist;
    if(abs(dist) < thre){
      set_angle_count[ch]++;
      servo_write(ch, 0);
      Rdata[ch].rvel = 0.0;
      continue;
    }
    // linear, min, not use cthre
    vel = min(vel, float(25.0 + 175.0 / 45.0 * (abs(dist) - 5.0))); 
    // vel = min(vel, float(100.0 + 0.4 * 175.0 / 45.0 * (abs(dist) - 24.0))); // velが大きいところでは早めにストップする
    if(dist < 0) vel *= -1.0;
    servo_write(ch, vel2pulse(ch, vel));
   
    Rdata[ch].rvel = vel;
    set_angle_count[ch] = 0;
  }
}

float wire2angle(int ch, float w){
  float angle_goal_tmp = angle_init_pose[ch] +
    (float)pull_direction[ch] * (w - wire_init_pose[ch]) / r_pulley * 180.0 / PI;
  return angle_goal_tmp;
}

float angle2wire(int ch, float agl){
  float wire_goal_tmp = wire_init_pose[ch] +
    (float)pull_direction[ch] * (agl - angle_init_pose[ch]) * r_pulley * PI / 180.0;
  return wire_goal_tmp;
}

void servo_write(int ch, int p){ //動かすサーボチャンネルと角度を指定
  if(p > 100) p = 100;
  if(p < -100) p = -100;
  p = map(p, -100, 100, SERVOMIN, SERVOMAX); //角度（0～180）をPWMのパルス幅（150～600）に変換
  if(ch < 5){
    pwm.setPWM(15-ch, 0, p);
  }else if(ch<10){
    pwm2.setPWM(ch-5, 0, p);
  }else{ // wheel
    if(ch == 10){ // right wheel
      pwm.setPWM(wheel_motor_num[0] , 0, p);
    }else{ // left wheel
      pwm2.setPWM(wheel_motor_num[1] , 0, p);
    }
  }
  //delay(1);
}


// enc、角度の初期化
void init_enc() {
  int init_value = digitalRead(init_pin);
  bool wire_check_tmp = true;
  if(init_value == 0){ //init
    for(int i=0;i<n;i++){
      // servo_zero[i] = muxRead(i); 
      servo_zero[i] = analogRead(enc_pin[i]);
      servo_n[i] = 0;
      enc[i] = servo_zero[i];
      enc_raw[i] = enc[i];
      angle[i] = ((float)enc[i]) / (float)maxV * 360.0;
      set_angle_count[i] = 0;
      if(abs(angle[i] - angle_init_pose[i]) > 50){
        wire_check_tmp = false;
      }
    }
    // init成功
    init_done = true;
    wire_init_check = wire_check_tmp;
  }
}

void init_enc_allrange() {
  int init_value = digitalRead(init_pin);
  // int init_value = 0; // force to initialize !!!!!
  bool wire_check_tmp = true;
  if(init_value == 0){ //init
    // pulley initialize
    for(int i=0;i<n;i++){
      // servo_zero[i] = muxRead(i); 
      servo_zero[i] = analogRead(enc_pin[i]);
      enc_raw[i] = servo_zero[i];

      float min_dist = 10000;
      int min_dist_idx = 0;
      for(int j=-1;j<2;j++){
        int enc_next = maxV * j + enc_raw[i];
        float angle_next = ((float)enc_next) / (float)maxV * 360.0;
        float angle_next_distance = abs(angle_next - angle_init_pose[i]);
        if(angle_next_distance < min_dist){
          min_dist = angle_next_distance;
          min_dist_idx = j;
        }
      }
      
      servo_n[i] = min_dist_idx;
      
      enc[i] = servo_n[i] * maxV + enc_raw[i];
      angle[i] = ((float)enc[i]) / (float)maxV * 360.0;
      set_angle_count[i] = 0;
      if(abs(angle[i] - angle_init_pose[i]) > 50){
        wire_check_tmp = false;
      }
    }
    // wheel initialize
    for(int i=10;i<12;i++){
      servo_zero[i] = analogRead(wheel_enc_pin[i-10]);
      servo_n[i] = 0;
      enc[i] = servo_zero[i];
      enc_raw[i] = enc[i];
      angle[i] = ((float)enc[i]) / (float)maxV * 360.0;
    }
    // init成功
    // init_done = true; // normal
    init_done = wire_check_tmp; // wire_check mode
    wire_init_check = wire_check_tmp;
  }
}

// エンコーダをよむ
// encはenc_raw, servo_n, enc, angleの4つの値で表される
void read_enc() {
  // 何周目かの更新
  for(int i=0;i<12;i++){
    // int enc_r = analogRead(i);
    // int enc_r = muxRead(i);
    // int enc_r = analogRead(enc_pin[i]);
    int enc_r;
    if(i<10){ // pulley
      enc_r = analogRead(enc_pin[i]);
    }else{ // wheel
      enc_r = analogRead(wheel_enc_pin[i-10]);
    }
    if(enc_r < 0) enc_r = 0;
    if(enc_r > maxV) enc_r = maxV;
    int min_dist = 10000;
    int min_dist_idx = 1;
    for(int j=0;j<3;j++){
      int enc_next = maxV * (servo_n[i]+j-1) + enc_r;
      int enc_next_distance = abs(enc_next - enc[i]);
      if(enc_next_distance < min_dist){
        min_dist = enc_next_distance;
        min_dist_idx = j;
      }
    }
    enc_raw[i] = enc_r;
    servo_n[i] += (min_dist_idx - 1);
    enc[i] = servo_n[i] * maxV + enc_raw[i];
    angle[i] = ((float)enc[i]) / (float)maxV * 360.0;
  }
}

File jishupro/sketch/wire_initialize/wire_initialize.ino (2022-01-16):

#include <Wire.h>
#include <PCA9685.h>            //PCA9685用ヘッダーファイル（秋月電子通商作成）

PCA9685 pwm = PCA9685(0x40);    //PCA9685のアドレス指定（アドレスジャンパ未接続時）
PCA9685 pwm2 = PCA9685(0x41);

// パルスの割合
// 4096がmax
// パルス幅1000-2000usecが動く範囲
#define SERVOMIN 246            //最小パルス幅 (標準的なサーボパルスに設定)
#define SERVOMAX 492            //最大パルス幅 (標準的なサーボパルスに設定)

const int n=10; // サーボのこすう

const int init_pin = 2; // サーボ初期化スイッチ入力
int servo_zero[10]; // サーボの初期角度
int servo_n[10]; // サーボのかいてんすう、最初0をかていする
int enc[10]; // エンコーダの値
int enc_raw[10]; // エンコーダの生の値
float angle[10]; // 角度 deg
bool init_done = false;
const int maxV = 4096;

// deg/s
float vel_limit_max[10] = {16.0,16.0,16.0,16.0,16.0,16.0,16.0,16.0,16.0,16.0};
float vel_limit_min[10] = {-20.-20,-20,-20,-20,-20,-20,-20,-20,-20,-20};
// pulse (-100 to 100)
int pulse_limit_max[10] = {17,17,17,17,17,17,17,17,17,17}; 
int pulse_limit_min[10] = {-8,-8,-8,-8,-8,-8,-8,-8,-8,-8};

int set_angle_count[10];
int set_angle(int ch, float vel, float theta, float cthre = 30.0, float thre = 3.0);

float vels[30]; // 速度測定用

/*
const int s0 = 32;
const int s1 = 25;
const int s2 = 34;
const int s3 = 39;
const int SIG_PIN = 36;
*/

const int enc_pin[10] = {36, 39, 34, 35, 32, 33, 25, 26, 27, 14};
// const int enc_pin[10] = {36, 39, 34, 35, 32, 14, 27, 26, 25, 33};


const int wheel_enc_pin[2] = {4, 0};

const int wheel_motor_num[2] = {7 , 7};

void setup() {
 pwm.begin();                   //初期設定 (アドレス0x40用)
 pwm.setPWMFreq(60);            //PWM周期を60Hzに設定 (アドレス0x40用)
 pwm2.begin();                   //初期設定 (アドレス0x40用)
 pwm2.setPWMFreq(60);            //PWM周期を60Hzに設定 (アドレス0x40用)
 pinMode(init_pin, INPUT_PULLUP);
 /*
 pinMode(s0, OUTPUT);
 pinMode(s1, OUTPUT);
 pinMode(s2, OUTPUT);
 pinMode(s3, OUTPUT);
 */
 Serial.begin(9600);
 Serial.println("Serial Start");
 for(int i=0;i<12;i++){
    servo_write(i, 0);
 }

 while(!init_done){
    init_enc();
    Serial.println("waiting initialization");
 }

 for(int i=0;i<12;i++){
    servo_write(i, 0);
 }
}

// 時計回りが正

void loop() {
  read_enc();
  bool check_initialize = true;
  for(int i=0;i<n;i++){
    Serial.print(String(angle[i]));
    if(i < n-1)Serial.print(", ");
    if(angle[i] < 60 || angle[i] > 300){
      check_initialize = false;
    }
  }
  Serial.println("      n=" + String(n));

  /*
  for(int i=0;i<n;i++){
    Serial.print(String(servo_zero[i]) + " ");
  }
  Serial.print("\n");
  */
  delay(100);  
}

// vel[deg/s] to pulse in (-100,100)
int vel2pulse(int ch, float vel){
  int pulse = 0;
  if(vel >= vel_limit_max[ch]){
    pulse = pulse_limit_max[ch];
    pulse += (int)((vel - vel_limit_max[ch]) / 3.7);
  }else if(vel <= vel_limit_min[ch]){
    pulse = pulse_limit_min[ch];
    pulse += (int)((vel - vel_limit_min[ch]) / 3.7);
  }
  return pulse;
}

float calc_speed(int ch, int p){
  servo_write(ch, p);
  for(int i=0;i<20;i++){
    read_enc();
    delay(100);
  }
  // Serial.print("Start calc: servo " + String(ch) + ", p=" + String(p) + "\n");
  unsigned long tm0 = micros();
  float ang0 = angle[ch];
  for(int i=0;i<20;i++){
    read_enc();
    delay(100);
  }
  unsigned long tm1 = micros();
  float ang1 = angle[ch];
  unsigned long tm = tm1 - tm0;
  float ang_diff = ang1 - ang0;
  float vel = ang_diff / (float)(tm / 1000000.0);
  Serial.print("ch " + String(ch) + ", p " + String(p) + ", vel " + String(vel) + "\n");
  // Serial.print("tm is " + String(tm) + " angle is " + String(ang_diff) + ", vel is " + String(vel));
  // Serial.print("\n");
  // Serial.println(vel);
  for(int i=0;i<5;i++){
    read_enc();
    delay(100);
  }
  servo_write(ch, 0);
  return vel;
}

// set servo to theta, vel > 0
// use in loop
// thre: end threshold
// cthre: control start threshold
int set_angle(int ch, float vel, float theta, float cthre, float thre){
   float dist = theta - angle[ch];
   if(abs(dist) < thre){
    set_angle_count[ch]++;
    servo_write(ch, 0);
    return set_angle_count[ch];
   }
   if(abs(dist) > cthre){
     if(dist < 0)vel = -vel;
     servo_write(ch, vel2pulse(ch, vel));
   }else{
    // dist<=cthreの場合
    /* // シンプル
    vel = 50 *(dist / cthre);
    servo_write(ch, vel2pulse(ch, vel));
    */ 
    // 線形
    float vel_max_tmp = 50.0;
    if(dist > 0){
      vel = vel_limit_max[ch] + (vel_max_tmp - vel_limit_max[ch]) * dist / cthre;
    }else{
      vel = vel_limit_min[ch] + (vel_max_tmp + vel_limit_min[ch]) * dist / cthre;
    }
    servo_write(ch, vel2pulse(ch, vel));
   }
   set_angle_count[ch] = 0;
   return set_angle_count[ch];
}

/* pulley only
void servo_write(int ch, int p){ //動かすサーボチャンネルと角度を指定
  if(p > 100) p = 100;
  if(p < -100) p = -100;
  p = map(p, -100, 100, SERVOMIN, SERVOMAX); //角度（0～180）をPWMのパルス幅（150～600）に変換
  if(ch < 5){
    pwm.setPWM(15-ch, 0, p);
  }else{
    pwm2.setPWM(ch-5, 0, p);
  }
  //delay(1);
}
*/

// pulley and wheel
void servo_write(int ch, int p){ //動かすサーボチャンネルと角度を指定
  if(p > 100) p = 100;
  if(p < -100) p = -100;
  p = map(p, -100, 100, SERVOMIN, SERVOMAX); //角度（0～180）をPWMのパルス幅（150～600）に変換
  if(ch < 5){
    pwm.setPWM(15-ch, 0, p);
  }else if(ch<10){
    pwm2.setPWM(ch-5, 0, p);
  }else{ // wheel
    if(ch == 10){ // right wheel
      pwm.setPWM(wheel_motor_num[0] , 0, p);
    }else{ // left wheel
      pwm2.setPWM(wheel_motor_num[1] , 0, p);
    }
  }
  //delay(1);
}

/*
int muxRead(int m){
  digitalWrite(s0, (m>>0 & 1));
  digitalWrite(s1, (m>>1 & 1));
  digitalWrite(s2, (m>>2 & 1));
  digitalWrite(s3, (m>>3 & 1));
  delay(10);
  return analogRead(SIG_PIN);
}
*/

// enc、角度の初期化
void init_enc() {
  int init_value = digitalRead(init_pin);
  if(init_value == 0){ //init
    for(int i=0;i<n;i++){
      // servo_zero[i] = muxRead(i); 
      servo_zero[i] = analogRead(enc_pin[i]);
      servo_n[i] = 0;
      enc[i] = servo_zero[i];
      enc_raw[i] = enc[i];
      angle[i] = ((float)enc[i]) / (float)maxV * 360.0;
      set_angle_count[i] = 0;
    }
    // init成功
    init_done = true;
  }
}

// エンコーダをよむ
// encはenc_raw, servo_n, enc, angleの4つの値で表される
void read_enc() {
  // 何周目かの更新
  for(int i=0;i<n;i++){
    int enc_r = analogRead(enc_pin[i]);
    // int enc_r = muxRead(i);
    if(enc_r < 0) enc_r = 0;
    if(enc_r > maxV) enc_r = maxV;
    int min_dist = 10000;
    int min_dist_idx = 1;
    for(int j=0;j<3;j++){
      int enc_next = maxV * (servo_n[i]+j-1) + enc_r;
      int enc_next_distance = abs(enc_next - enc[i]);
      if(enc_next_distance < min_dist){
        min_dist = enc_next_distance;
        min_dist_idx = j;
      }
    }
    enc_raw[i] = enc_r;
    servo_n[i] += (min_dist_idx - 1);
    enc[i] = servo_n[i] * maxV + enc_raw[i];
    angle[i] = ((float)enc[i]) / (float)maxV * 360.0;
  }
}

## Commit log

2021-12-24 add CAD
    [FB5311M.SLDPRT, assem_set_motor.SLDASM, base.DXF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]
2021-12-24 add small stl
    [link_leg_small.STL]
2021-12-24 add foot_small
    [link_foot_small.STL]
2021-12-24 add foot_m
    [link_foot_m.STL, link_leg_m.STL]
2021-12-24 add models
    [sample_model.urdf]
2021-12-25 change origin
    [link_foot.SLDASM, link_leg.SLDASM]
2021-12-25 add some stl
    [link_foot.SLDASM, shoulder2.SLDPRT, shoulder2.STL]
2021-12-25 add root
    [base_motor.SLDASM, knee.SLDASM, leg.SLDASM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]
2021-12-25 add l
    [link_leg.SLDASM, link_leg_l.SLDASM, link_leg_l.STL]
2021-12-25 add eus model
    [sample_model.urdf]
2021-12-25 add wire-calc
    [mbot.urdf, sample_model.urdf]
2021-12-26 add esp32
2021-12-30 addd some cad
    [base_motor.SLDASM, connector_45.SLDPRT, foot_simple.SLDPRT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]
2022-01-04 change models
    [assem_set_motor.SLDASM, assem_shoulder.SLDASM, base_motor.SLDASM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]
2022-01-04 change model unit
    [assem_shoulder.SLDASM, base_motor.SLDASM, knee.SLDASM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]
2022-01-04 add arduino code
2022-01-04 change initial value of wire length
    [mbot.urdf, sample_model.urdf]
2022-01-06 add circuit
    [PCA9685.SLDPRT, assem_shoulder.SLDASM, base_motor.SLDASM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]
2022-01-07 change encoder idx and motor num
    [mbot_gazebo.urdf, mobile_robot.urdf]
2022-01-09 add motor adjust
2022-01-10 change wire pull
2022-01-11 add wheel
    [assem_shoulder.SLDASM, base_motor.SLDASM, circuit.SLDASM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]
2022-01-11 add wheel program of esp32
2022-01-13 add camera mount
    [assem_shoulder.SLDASM, base_motor.SLDASM, camera_mount.SLDPRT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]
2022-01-16 change wire init algo
